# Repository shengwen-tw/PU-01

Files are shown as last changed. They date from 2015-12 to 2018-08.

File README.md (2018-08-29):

## PU-01

**PU-01** was designed by me in the class of **"Fundamentals of Unmanned Aerial Vehicle System Design"** back in 2016.

It is a twin boom fixed wing aircraft with a pusher setup and can be controlled manually by human on ground.

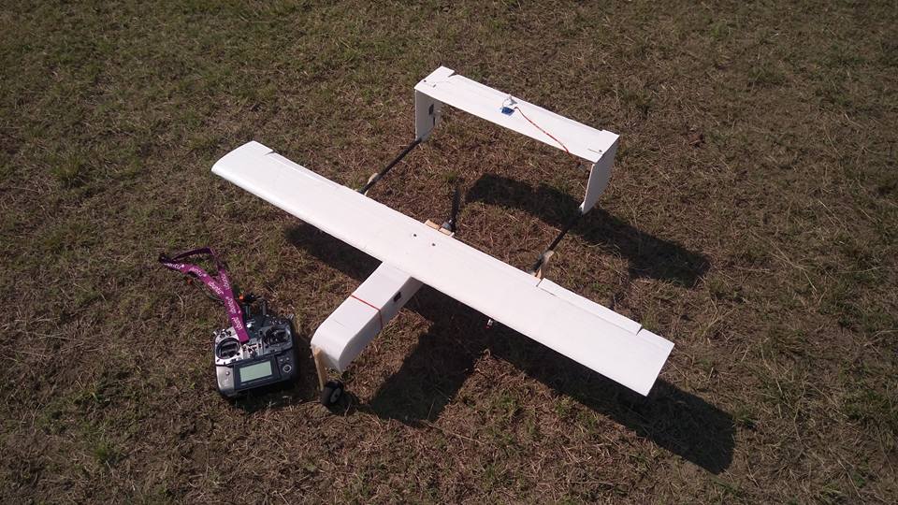
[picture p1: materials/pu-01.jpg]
</a>

## Specification

| Parameter | |
|:---|:---|
| Cruise speed | 52km/hr  |
| Max take-of weight | 1.2kg |
| Wing airfoil  | Clark-Y  |
| Wing span | 1.13m |
| Tail airfoil  | NACA0015 |
| Motor | 1400kv |
| Propeller | 8060 |

## Demonstrations

**PU-01 - Maiden Flight (without landing gear)**

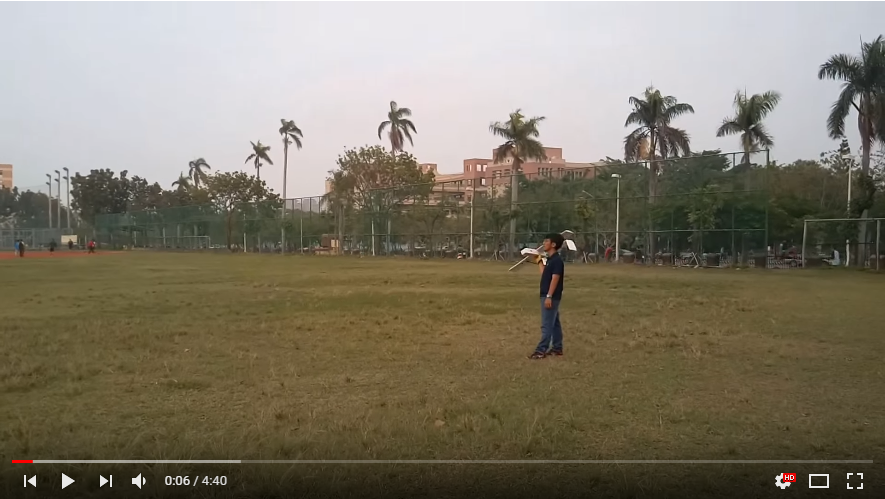
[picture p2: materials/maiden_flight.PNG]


**PU-01 - Second Flight (with landing gear)**

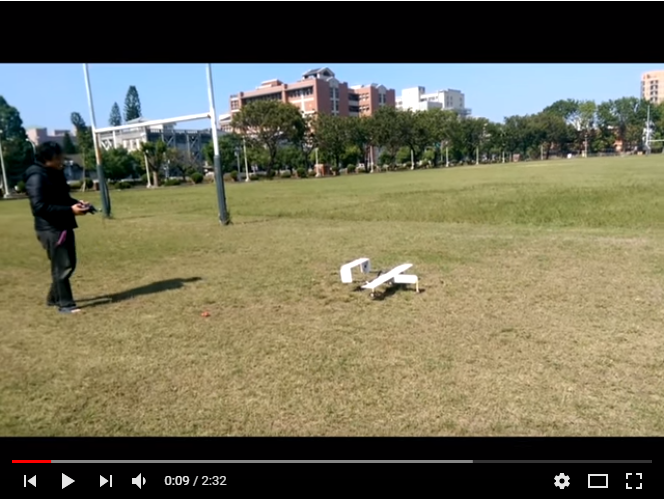
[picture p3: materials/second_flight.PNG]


**PU-02 - Stability analysis using XFLR5**

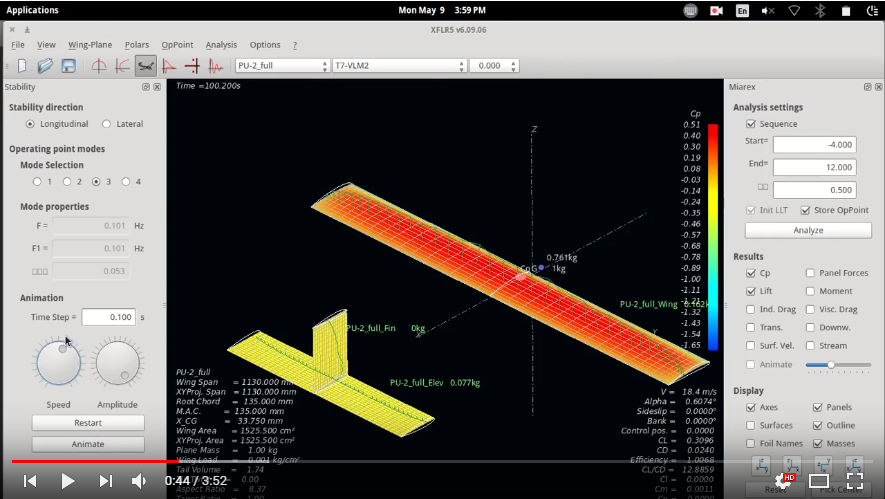
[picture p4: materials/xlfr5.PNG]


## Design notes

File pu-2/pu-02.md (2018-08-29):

## PU-02

Wing chord: 14.5cm

V-tail chord: 12cm

H-tail chord: 11cm

Control surface width: 30%

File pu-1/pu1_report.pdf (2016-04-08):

## 交通大學 無人飛機設計導論期末作品

指導教授：太空中心 陳彥升博士
協助指導：成功大學航太系林清一教授實驗室
設計者：靜宜大學 鄭聖文

### 一.各項飛行參數及設計

飛機名稱：PU-01 (PU = Providence University) 類型：Twin boom (Pusher)

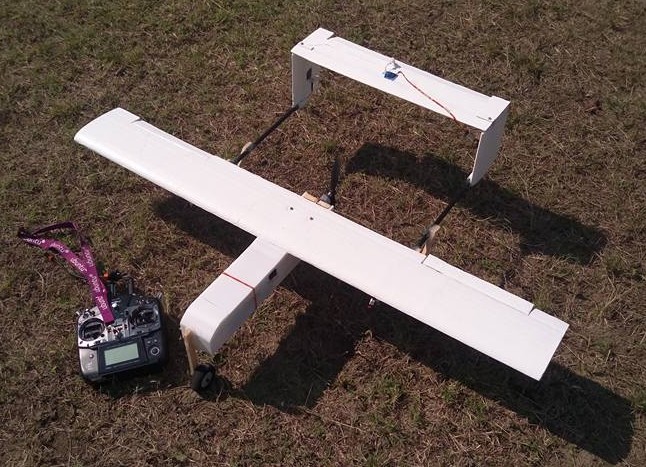
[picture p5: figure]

基本飛行參數
巡航速度 | 52 km/hr
最大起飛重量 | 1.2 kg
巡航時間 | - (第四次試飛時損毀)

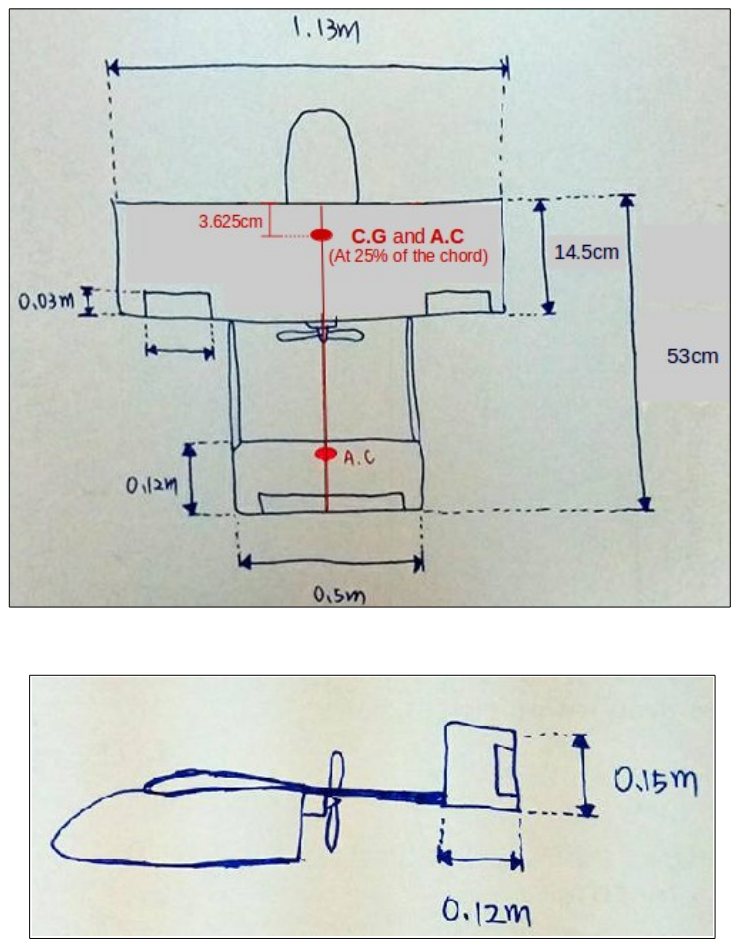
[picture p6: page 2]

主翼參數
翼型 | Clark Y
翼面積 | 0.16385 m²
翼展 | 1.13 m
弦長 | 0.145 m
展弦比 | 7.8

水平尾翼參數
翼型 | Clark Y (嚴重設計錯誤)
翼面積 | 0.06m²
翼展 | 0.5 m
弦長 | 0.12 m
展弦比 | 4.2

垂直尾翼參數
翼型 | NACA0015
翼面積 | 0.018 m²
翼展 | 0.15 m
弦長 | 0.12 m
展弦比 | 1.25

動力系統參數
馬達性能 | 1400 kv
螺旋槳規格 | 8060

### 二.設計缺點

看到首次設計的飛機能夠順利飛行，相當開心，不過因為初次設計遙控飛 機的關係，犯了幾項相當不好的錯誤，分別為：

1.使用模擬軟體估算翼型 CL3d 值時，錯誤的使用了 CL2 d 帶入 Lift equation 計算主翼面積，導致升力被高估了許多，起飛重量不如預期。

2.挑選水平尾翼翼型時，誤用了非對稱翼型 Clark Y，而非 NACA0015 或 NACA0012 等對稱翼翼型，導致首次測試時，即使將飛機升降舵打平到了極 限，也無法產生一個向上的俯仰角，使飛機直接撞擊地面
解決方案：翻轉水平尾翼，使平滑面朝向天空，並做些許調整解決問題

3.機身設計時，沒有預留好調整重心的空間，導致必須使用兩顆電池並聯增加 重量。由於額外的重量，使飛機更不易操縱。

4.本架飛機各部份的接合點，使用不少 3D 列印的零件，然而零件設計上的一 些缺點，與結構本身之強度並沒有預期的好，導致第一次墜毀後，只能以熱 溶膠黏死。下次設計飛機時，會謹慎考慮是否使用 3D 列印。

5.由於水平尾翼沒有很精確的擺置正確的位置，導致飛機擁有向右滾轉的傾 向，使操控者不時需要調整滾轉角達到平衡

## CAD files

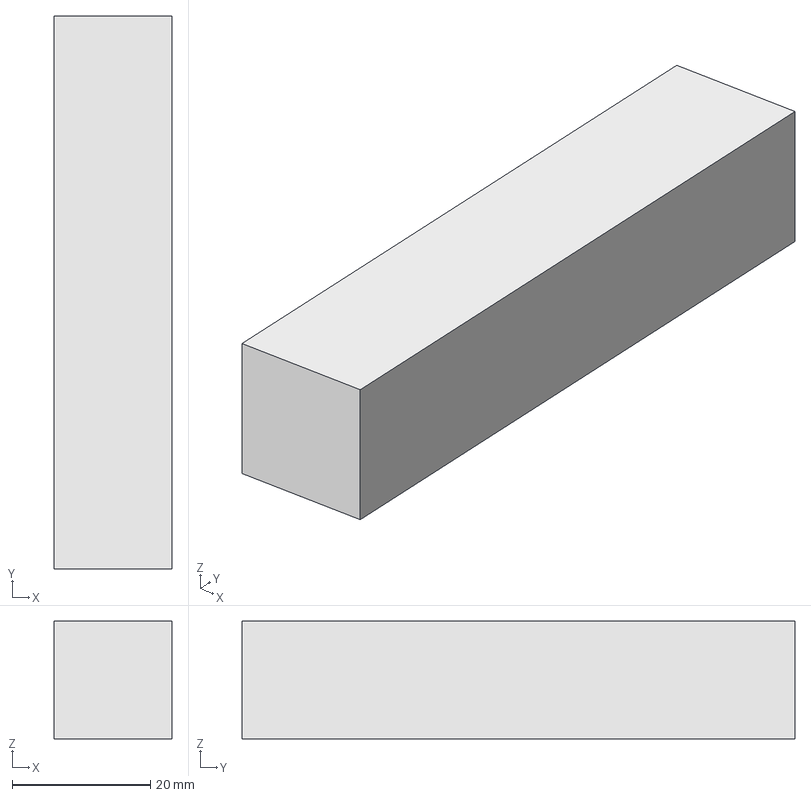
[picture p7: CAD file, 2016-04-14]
pu-2/3d_model/connector_no_drill.fcstd
17.0 x 80.0 x 17.0 mm

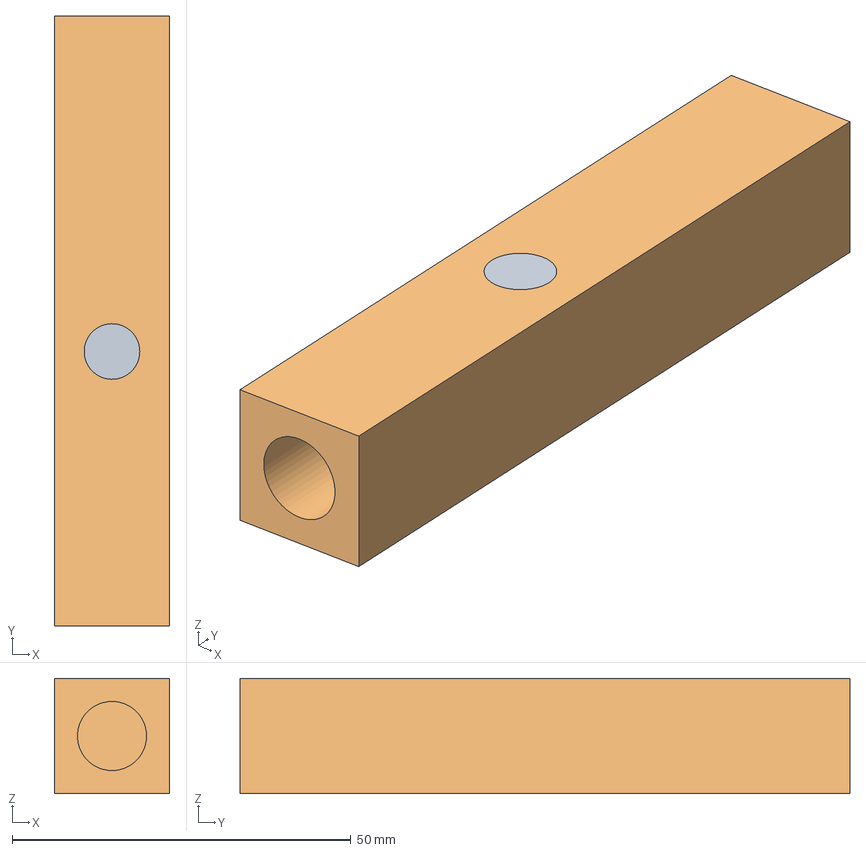
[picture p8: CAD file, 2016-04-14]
pu-2/3d_model/connector.fcstd
17.0 x 90.0 x 17.0 mm

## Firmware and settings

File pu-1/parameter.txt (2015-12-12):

__________________________________________________
wing span = 1.13
wing chord = 0.15
wing area = 0.1695
wing Aspect ratio= 7.53333333333
__________________________________________________
Wing control surface chord = 3.0cm
Wing control surface left edge = 16.95cm
Wing control surface right edge = 33.9cm
__________________________________________________
CL(0) = 0.617 <--- 3D
Cruise speed = 16.77m/s
air density = 1.225
Takeoff weight = 1.83823490821
__________________________________________________
Static margin = 0.1
Length from C.G to wing A.C = 1.5cm
__________________________________________________
Horizontal tail area: 0.0381375m^2
Horizontal tail span: 39.0576496989cm
Horizontal tail chord: 9.76441242472cm
__________________________________________________
Vertical tail area: 0.0119709375m^2 <--- Twin fin
Vertical tail span: 12.2597622666cm
Vertical tail chord: 9.76441242472cm
Vertical tail AR: 1.25555555556
__________________________________________________
Spar1 position = 0.2825
Spar2 position = 0.8475
Length between spars = 0.565
__________________________________________________

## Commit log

2015-12-12 Add parameter list
    [parameter.txt]
2016-01-04 Add stall speed calculation
2016-04-08 Catagorize different aircraft
    [parameter.txt]
2016-04-08 Add tail connector
    [connector_no_drill.fcstd]
2016-04-14 Create 3d model directory
    [connector.fcstd, connector_no_drill.fcstd]
